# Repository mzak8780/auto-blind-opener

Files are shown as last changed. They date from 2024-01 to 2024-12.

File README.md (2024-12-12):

# Automatic Blind Opener Project
This project consists of the planning, design, build, and testing of an automatic blind opener. 

The design is an adaptation of the following project: https://www.the-diy-life.com/arduino-automatic-blind-opener-works-with-a-remote-control-alexa/.

Customizations were applied to fit the requirements of my particular blinds and window layout.

The blind opener is voice-controlled via the use of a universal RF hub and an Alexa puck.

## Blind Opener Project Sheet

| Part Name | Supplier | Cost ($) | Comments |
|---|---|---|---|
| 0.4Nm Stepper Motor -> Nema 17 | Ebay | 15 | Sized down to a smaller stepper motor for size, weight, and cost benefits. Incorporated gear design to compensate for power loss. |
| Stepper Motor driver (5 pack) | Ebay | 10.50 | |
| Infrared sensor with remote | Ebay | 7.50 | Had to purchase a second sensor as I shorted the first. |
| 2.1 DC Input power module | Jaycar | 3 | |
| Pro Micro Arduino Board | Ebay | 15 | |
| Smart Infrared Remote | Ebay | 20 | |
| Capacitor | Jaycar | <1 | |
| Resistor | Jaycar | <1 | |
| Bearings | Amazon | 10 | 

### Gear Design
As calculated, the torque required to turn the blinds from a closed -> open position requires:
0.735Nm
To minimize size, cost, and weight, I chose a 0.4Nm holding torque stepper motor which has an active torque of 0.34Nm. Rounding this down to ensure tolerance, we assume the stepper has a torque of 0.3 Nm. To counter this loss in force, I implemented a gear design to increase output torque. The input gear will have 13 teeth to the output gear which will have 36 teeth. This equates to a torque multiplication of:
$36/13 = 2.76$ approx.
Meaning I will receive an output torque of:
$2.76 * 0.3 = 0.828Nm$.
Which should suffice in moving the roller blinds in both directions without the need for a counterweight.

The larger output gear will be 3D printed with a beaded circular component in which the thread of the roller blind will wrap around. This set will be rotated around a standard 22x7x8 bearing on a M8 screw-acting shaft.

### Blind Opener Case Design
The blind opener would be designed to be compact and subtle. The encloser would house the Nema17 stepper motor as well as the control electronics. It would have openings for the power supply, the USB-C port for the microcontroller as well as the RF sensor. The lid, base, and motor would be joined with M3 screws. Small shelves would be designed to hold the Arduino board and the motor driver board. Below is the first assembly design of the blind opener. 
Torque Insufficiencies
With the above design, the torque was adequate to close the blinds however was unable to open them. The force and friction of the gears impact the output of force and therefore more torque is required. After acquiring a 3D printer of my own, I was able to research and experiment with various gearboxes to maximize torque output without altering the hardware I had already purchased.

<p align="center">
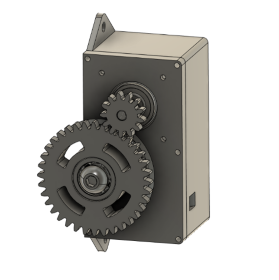
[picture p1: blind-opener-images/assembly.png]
  
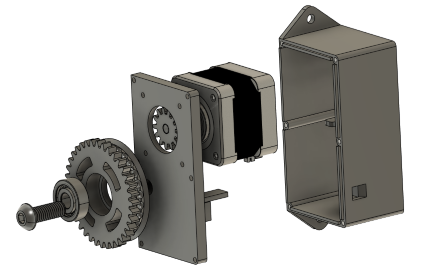
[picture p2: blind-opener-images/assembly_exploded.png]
  
</p>

<p align="center">
  <em>Figure 1 & 2: Blind Opener V1 CAD Assembly</em>
</p>

### Planetary Gearbox 3.7:1
Utilizing the plethora of designs available online through the 3-D printing community, I began experimenting with planetary gearboxes to increase my output torque. I began by printing: https://www.printables.com/model/281222-nema17-planetary-gearbox which utilized hardware I already had and would theoretically increase my torque by 3.7 times. After printing and installing the gearbox, a similar issue was found where the output was still too low to open the blinds. 

<p align="center">
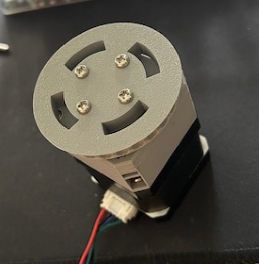
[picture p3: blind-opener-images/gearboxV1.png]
    
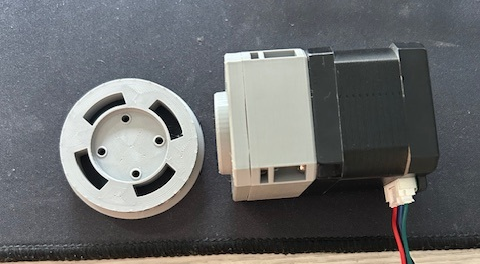
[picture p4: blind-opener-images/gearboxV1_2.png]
    
</p>

<p align="center">
  <em>Figure 3 & 4: Gearbox solution #1</em>
</p>

### Planetary Gearbox 25:1
After another failed design, I looked to overcompensate on the torque aspect and found an online design that amplified the torque by a ratio of 25:1 (https://www.printables.com/model/136854-25-1-ratio-planetary-gearbox-for-nema-17-stepper ). After purchasing some additional fasteners, I printed and assembled the gearbox for testing. Initial tests proved to be promising as the blinds were able to be opened however due to the lack of friction with the chain beads on the output spool, the chain would jump and skip output rotations. Additionally, the way the gearbox was designed, the front spool was attached to a bearing that simply clicked into the front face of the gearbox. To successfully pull the blinds open, the tension of the chain had to be quite taught which would cause the bearing to slip out of the frame.

<p align="center">
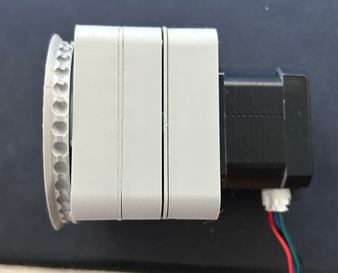
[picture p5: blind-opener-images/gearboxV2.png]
    
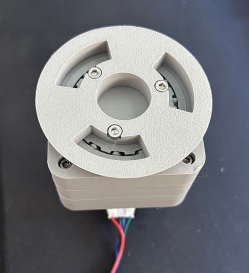
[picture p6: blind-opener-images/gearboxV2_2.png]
    
</p>

<p align="center">
  <em>Figure 5 & 6: Gearbox solution #2</em>
</p>

### Spool Design
The initial design of the spool mimicked the size of the blind’s chain mechanism. I measured the dimensions of the beaded chain and implemented a similar pattern into a spool on Fusion 360 (Figure 3). This was advantageous for initial testing however due to the skipping of beads under high load (blind opening), I sought to improve the design. I began by increasing the size of the spool as well as the distance between the bead housings within my design. This is because I noticed that when the rope was taught, the beads would not sit properly in their grooves. This improved traction however skipping was still frequent. I then turned to the design of the blind itself and replicated the box-like pattern (Figure 5). This way, the beads would simply get caught instead of having to fit a groove.

<p align="center">
  
  <em>Figure 7: Final spool solution</em>
</p>

### Final Build
After constructing the spool and attaching it to the gearbox and motor, the final step was to design a case to enclose the electronics. The case was fitted with 4 holes for wall mounting and a few additional holes for wire management. The electronics fit inside as seen in Figure 6. The final construction can be seen in Figure 7 and Figure 8.

<p align="center">
  
  <em>Figure 8: Electronics enclosed within casing</em>
</p>

<p align="center">
  
  
</p>
<p align="center">
  <em>Figure 9 & 10: Final build completed</em>
</p>

## Video Demonstration

https://github.com/mzak8780/auto-blind-opener/assets/50131251/77a8361b-64e1-4853-98c4-8377ad70cdca
<p align="center">
  <em>Video 1: Blind opening demonstration</em>
</p>

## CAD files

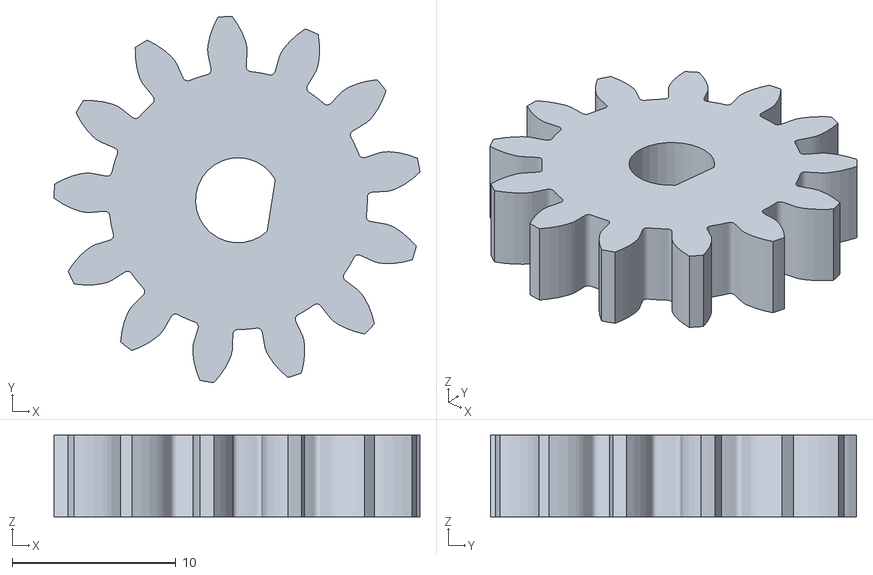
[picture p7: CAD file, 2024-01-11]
print-files/blind-opener-v1/gear-13-teeth.stl
22.4 x 22.4 x 5.00

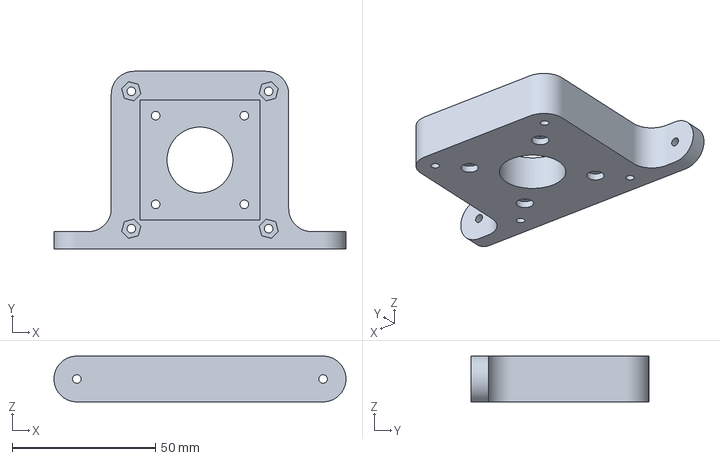
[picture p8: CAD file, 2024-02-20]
print-files/component-customisations/bot-wallbracket.3mf
102.0 x 62.0 x 16.0 mm

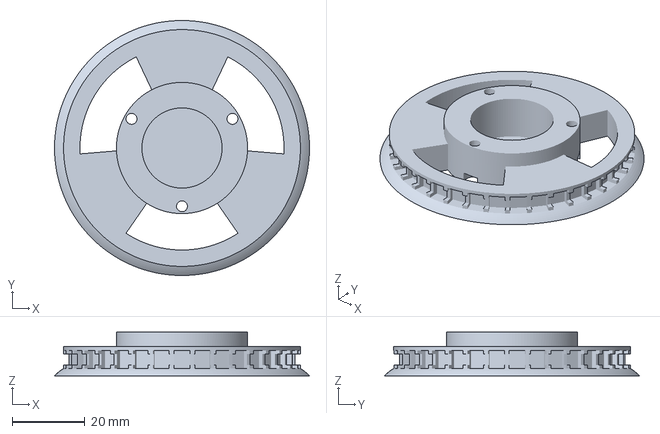
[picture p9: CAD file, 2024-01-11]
print-files/spool-attachments/spool-v5.3mf
70.0 x 70.0 x 12.0 mm

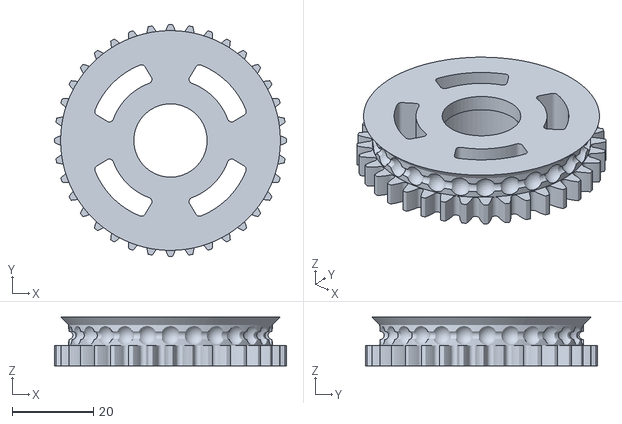
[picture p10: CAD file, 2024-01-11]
print-files/blind-opener-v1/gear-36-teeth.stl
57.0 x 57.0 x 12.0

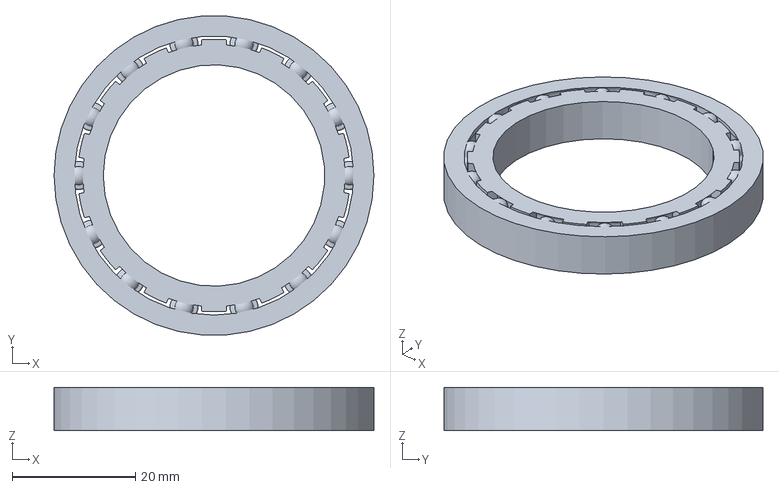
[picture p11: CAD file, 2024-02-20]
print-files/component-customisations/In_place_bearing_65.3mf
52.0 x 51.9 x 7.00 mm

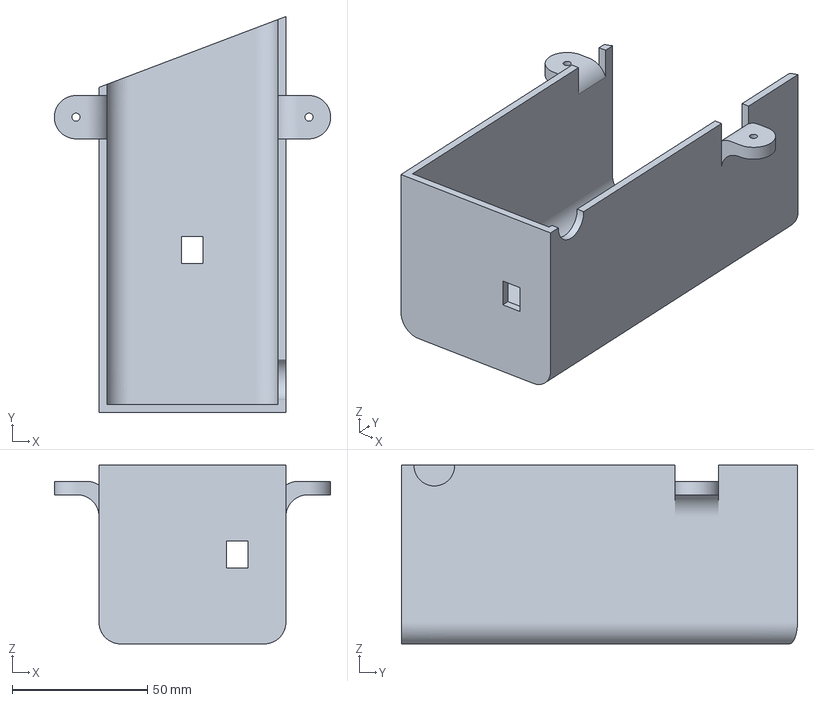
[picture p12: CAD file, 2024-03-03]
print-files/cover/coverV2.3mf
102.0 x 146.1 x 66.0 mm

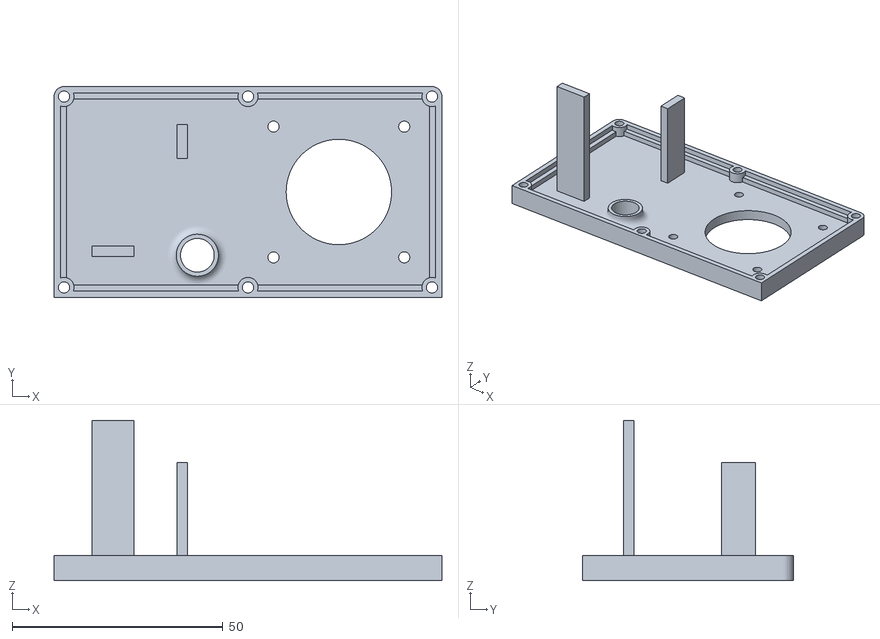
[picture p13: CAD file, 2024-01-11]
print-files/blind-opener-v1/lid.stl
92.0 x 50.0 x 38.0

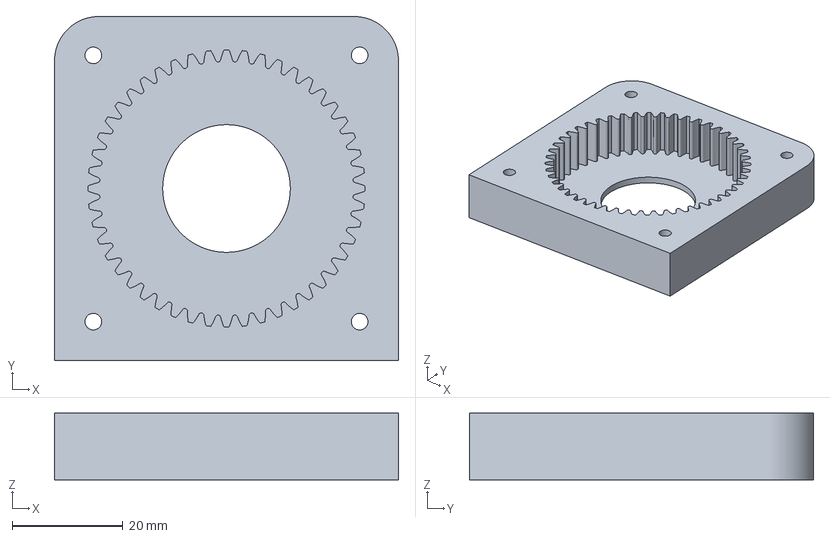
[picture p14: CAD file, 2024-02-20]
print-files/component-customisations/mid-wallbracket.3mf
62.0 x 62.0 x 12.0 mm

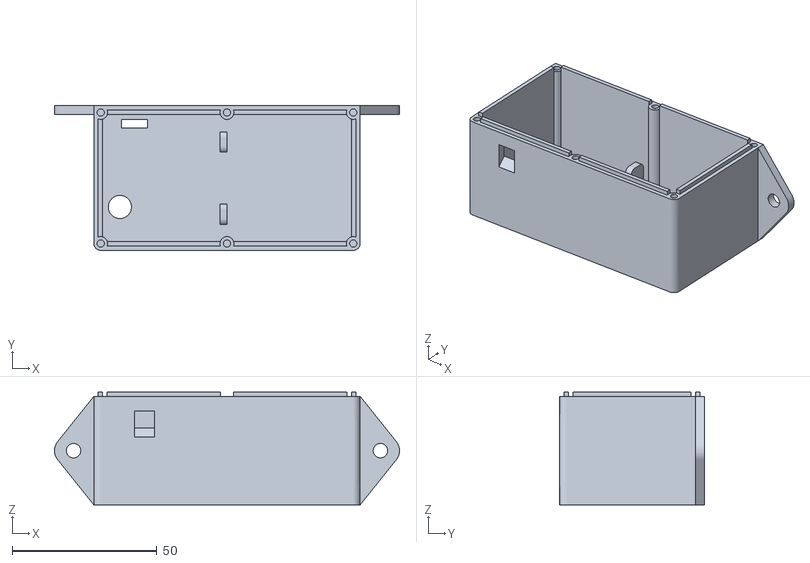
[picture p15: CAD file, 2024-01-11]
print-files/blind-opener-v1/base.stl
119.2 x 50.0 x 39.0

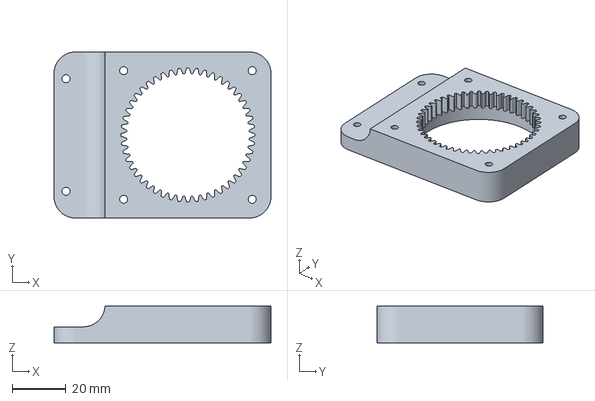
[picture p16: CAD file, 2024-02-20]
print-files/component-customisations/top-wallbracket.3mf
81.0 x 62.0 x 13.7 mm

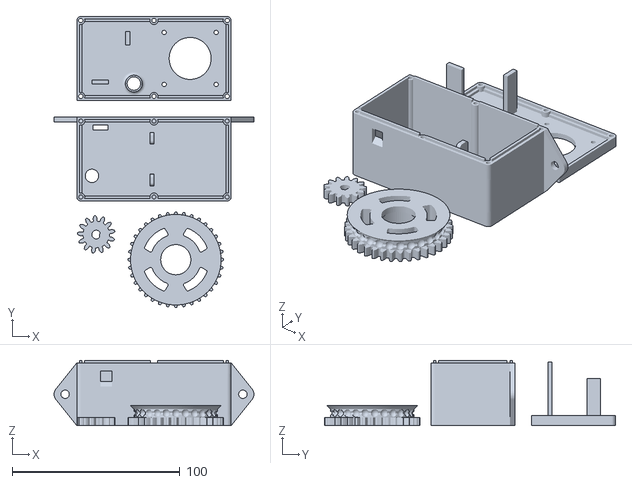
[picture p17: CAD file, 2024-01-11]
print-files/blind-opener-v1/blind-opener-all.stl
119.2 x 173.5 x 39.0

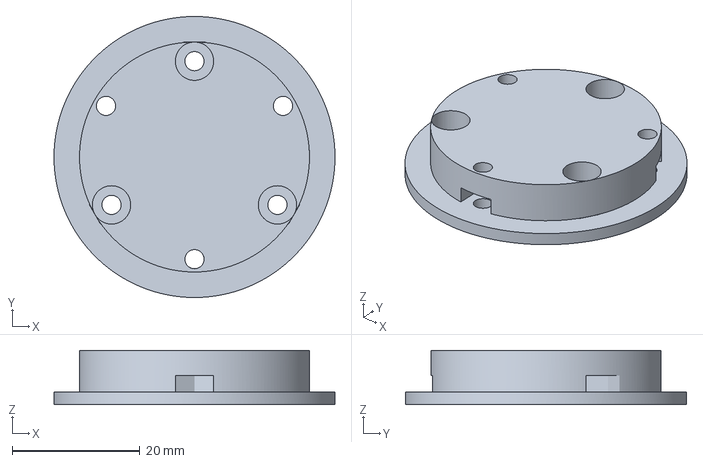
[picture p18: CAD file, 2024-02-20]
print-files/component-customisations/internal-driver.3mf
44.0 x 44.0 x 8.50 mm

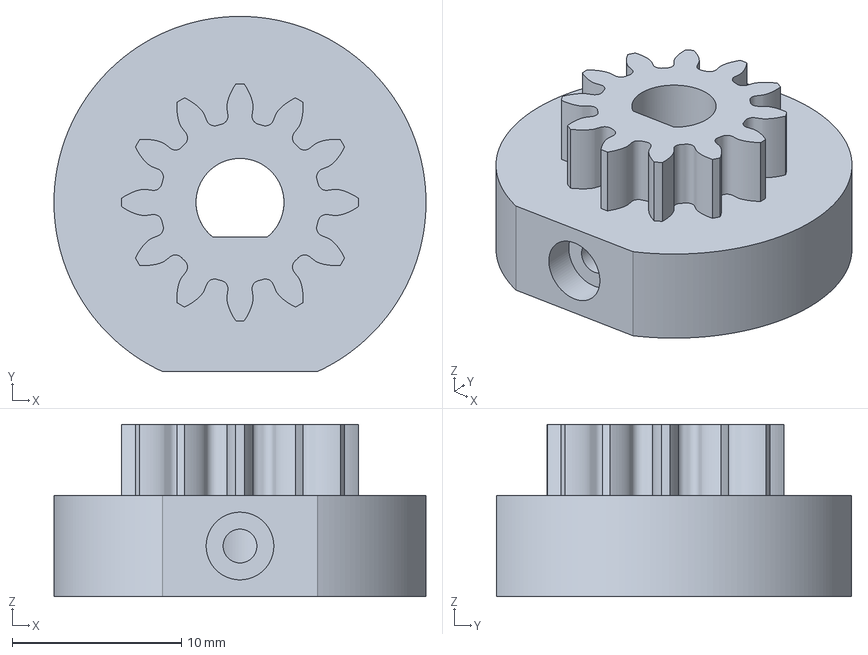
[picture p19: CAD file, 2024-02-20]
print-files/component-customisations/motor-driver.3mf
22.0 x 21.0 x 10.2 mm

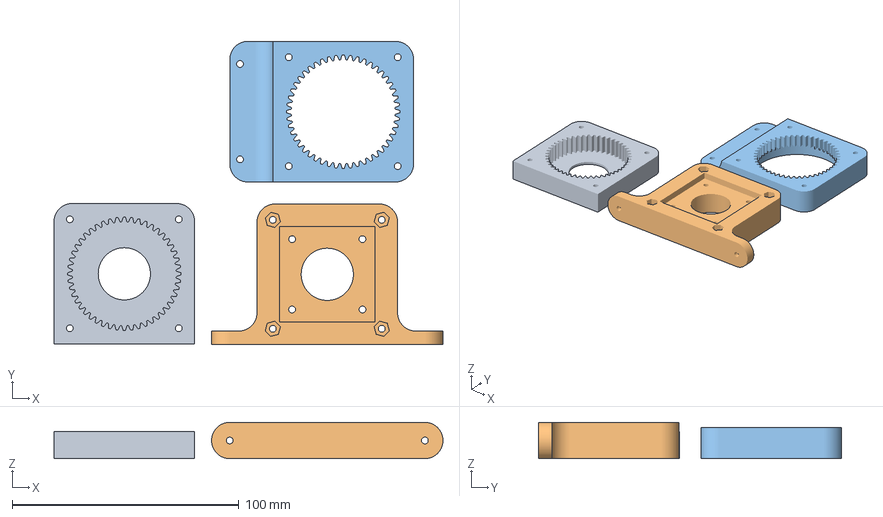
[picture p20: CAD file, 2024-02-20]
print-files/component-customisations/modified-gearbox.3mf
171.5 x 133.7 x 16.0 mm
mid.stl
bot.stl
top.stl

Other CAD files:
print-files/component-customisations/gear-v2.3mf
print-files/component-customisations/gear-driver.3mf
print-files/component-customisations/spool-attachment.3mf
print-files/cover/coverV1.3mf
print-files/spool-attachments/spool-v4.3mf

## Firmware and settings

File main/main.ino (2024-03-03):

// Include libraries
#include <IRremote.h>

// Define pins
const int IR_PIN = 10;
const int ENABLE_PIN = 9;
const int STEP_PIN = 1;
const int DIR_PIN = 0;

// Define blind parameters
const unsigned long BLIND_LENGTH = 94000;
const int BLIND_SPEED = 500;
unsigned long blindPosition = 0;
const int BLIND_DIR = 0;

// IR receiver object
IRrecv irrecv(IR_PIN);
decode_results results;

// Function prototypes
void setup();
void loop();
void driveMotor(unsigned long value);
void moveMotor(int moveDir, unsigned int noSteps);

void setup() {
  // Start the IR receiver
  irrecv.enableIRIn();
  
  // Set pin modes
  pinMode(ENABLE_PIN, OUTPUT);
  digitalWrite(ENABLE_PIN, HIGH); // Turn off motors
  pinMode(STEP_PIN, OUTPUT);
  pinMode(DIR_PIN, OUTPUT);
}

void loop() {
  if (irrecv.decode()) {
    auto value = irrecv.decodedIRData.decodedRawData;
    driveMotor(value);
    irrecv.resume();
    delay(200);
  }
}

void driveMotor(unsigned long value) {
  switch (value) {
    case 3108437760: // Button + Pressed - Open Slightly
      if (blindPosition >= 6000) {
        moveMotor(0, 6000);
        blindPosition -= 6000;
      }
      break;
    case 3927310080: // Button - Pressed - Close Slightly
      if (blindPosition <= BLIND_LENGTH - 6000) {
        moveMotor(1, 6000);
        blindPosition += 6000;
      } else {
        Serial.print("Blind position to closed at: ");
        Serial.print(blindPosition);
      }
      break;
    case 2907897600: // Button 0 Pressed - Open Fully
      moveMotor(0, blindPosition);
      blindPosition = 0;
      break;
    case 3910598400: // Button 1 Pressed - Close Fully
      moveMotor(1, BLIND_LENGTH - blindPosition);
      blindPosition = BLIND_LENGTH;
      break;
    case 3860463360: // Button 2 Pressed - Blind Preset 2 (1/4 Closed)
      if (blindPosition > BLIND_LENGTH / 4) {
        moveMotor(0, blindPosition - (BLIND_LENGTH / 4));
      } else if (blindPosition < BLIND_LENGTH / 4) {
        moveMotor(1, (BLIND_LENGTH / 4) - blindPosition);
      }
      blindPosition = BLIND_LENGTH / 4;
      break;
    case 4061003520: // Button 3 Pressed - Blind Preset 3 (1/2 Closed)
      if (blindPosition > BLIND_LENGTH / 2) {
        moveMotor(0, blindPosition - (BLIND_LENGTH / 2));
      } else if (blindPosition < BLIND_LENGTH / 2) {
        moveMotor(1, (BLIND_LENGTH / 2) - blindPosition);
      }
      blindPosition = BLIND_LENGTH / 2;
      break;
    case 3175284480: // Press # to reset blind position to 0 (open)
      blindPosition = 0;
      break;
    case 3041591040: // Press * to reset blind position to max blind length (closed)
      blindPosition = BLIND_LENGTH;
      break;

    default: // Handle unrecognized IR signals
      Serial.println("Unknown IR signal");
      break;
  }
}

void moveMotor(int moveDir, unsigned int noSteps) {
  digitalWrite(ENABLE_PIN, LOW); // Turn on motors
  delay(200);
  digitalWrite(DIR_PIN, moveDir == BLIND_DIR ? HIGH : LOW);
  for (unsigned int i = 0; i < noSteps; i++) {
    digitalWrite(STEP_PIN, HIGH);
    delayMicroseconds(BLIND_SPEED);
    digitalWrite(STEP_PIN, LOW);
    delayMicroseconds(BLIND_SPEED);
  }
  digitalWrite(ENABLE_PIN, HIGH); // Turn off motors
}
